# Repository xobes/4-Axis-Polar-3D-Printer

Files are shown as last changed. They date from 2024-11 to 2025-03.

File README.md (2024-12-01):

# 4 Axis Polar 3D Printer

This is my 4 axis, polar, "core-RΘ" 3D printer – an entirely new type of multi axis 3D printer designed from the ground up. 

Check out my [youtube video](https://www.youtube.com/watch?v=VEgwnhLHy3g) to see it in action!
Watch the video (https://www.youtube.com/watch?v=VEgwnhLHy3g)

### Slicer
A multi axis printer is pretty hopeless without a non-planar slicer, which is why I built this quick [radial slicer](https://github.com/jyjblrd/Radial_Non_Planar_Slicer) for the printer. This leverages the printer's rotating nozzle to print simple parts without supports, but there are some limitations to it which I cover in the YouTube video. I'm also working on an optimization based slicer which will be able to print any object without support so stay tuned for that!



### Assembly
You can view the [3d model online](https://a360.co/3VdXkRY) to see how to assemble the printer. Everything is 3D printable, however I got the extruder mount made out of metal by JLCPCB as there is quite a bit of torque on that part. I've also included the gerber files to make your own PCB buildplate, but a sheet of MDF wood would also work.

### BOM
Some links are included so you know what to get, but they are by no means the best source to get the parts.
| | Qty | | Note |
| --- | --- | --- | --- |
| Frame | | | |
| 2040 Extrusion 350mm | 1 | [Aliexpress](https://www.aliexpress.us/item/1005005037443914.html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) | |
| 2040 Extrusion 100mm | 1 | [Aliexpress](https://www.aliexpress.us/item/1005005037443914.html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) | |
| 2020 Extrusion 150mm | 1 | [Aliexpress](https://www.aliexpress.us/item/1005005037443914.html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) | |
| 2020 Extrusion 250mm | 1 | [Aliexpress](https://www.aliexpress.us/item/1005005037443914.html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) | |
| 2020 corner bracket | 10  | [Aliexpress](https://www.aliexpress.us/item/1005002883833150.html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) | |
| | | | |
| Hardware | | | |
| 2020 T Nuts | 50  | [Aliexpress](https://aliexpress.us/item/1005003023734101.html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) | |
| MGN9 250mm Rail | 1 | [Aliexpress](https://www.aliexpress.us/item/1005004908405311.html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) | |
| MGN12 250mm Rail | 2 | [Aliexpress](https://www.aliexpress.us/item/1005004908405311.html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) | |
| MGN9C Block | 2 | [Aliexpress](https://www.aliexpress.us/item/1005004908405311.html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) | |
| MGN12H Block | 2 | [Aliexpress](https://www.aliexpress.us/item/1005004908405311.html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) | |
| M4 Screw Set | | [Aliexpress](https://www.aliexpress.us/item/1005002109863123.html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) | |
| M3 Screw Set | | | Need 40mm screw |
| M3 Square Nut | 50  | [Aliexpress](https://www.aliexpress.us/item/1005001612157787.html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) | |
| MR85ZZ (5x8x2.5) | 4 | [Aliexpress](https://www.aliexpress.us/item/1005002702288640.html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) | B axis |
| 6810ZZ | 2 | [Aliexpress](https://www.aliexpress.us/item/32862403898.html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) | C axis |
| 5mm Rod 50mm length | | | B axis |
| 5mm Flange coupling | | | |
| 5x11x6 collet | 1 | [Aliexpress](https://www.aliexpress.com/item/1005005687346657.html?spm=a2g0o.order_list.order_list_main.270.6df81802pwJpHi) | B axis |
| | | | |
| Drive | | | |
| Nema 17 300mm Lead Screw | 1 | [Aliexpress](https://www.aliexpress.us/item/1005005575285492.html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) | |
| T8\*8 Lead Screw Nut | 1 | [Aliexpress](https://www.aliexpress.us/item/32957828816.html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) | |
| Nema 17 34mm | 3 | | |
| GT2 Belt Loop 410mm | 1 | | |
| GT2 Belt Loop 760mm | 1 | | |
| GT2 Pully 16T | 2 | [Aliexpress](https://www.aliexpress.us/item/1005004314084512.html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) | |
| GT2 Idler 16T w/o Teeth  | 4 | | |
| GT2 Pully 40T | 1 | | |
| GT2 Idler 16T w/ Teeth | 2 | [Aliexpress](https://www.aliexpress.us/item/32817328238.html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) | |
| | | | |
| Electronics | | | |
| Control Board | 1 | [Aliexpress](https://www.aliexpress.us/item/1005002372751834.html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) | |
| 24V 10A Power Brick | 1 | [Aliexpress](https://www.aliexpress.us/item/1005003088055215.html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) | |
| 5.5x2.5 plug | 1 | [Aliexpress](https://www.aliexpress.us/item/33034810979.html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) | |
| long nozzle | 1 | [Aliexpress](https://www.aliexpress.com/item/1005007437644929.html?spm=a2g0o.order_list.order_list_main.39.6df81802pwJpHi) | |
| aquarium pump | 1 | [Aliexpress](https://aliexpress.com/item/1005005987431203.html?spm=a2g0o.order_list.order_list_main.219.6df81802pwJpHi) | |
| BIQU H2 V2S extruder | 1 | [Aliexpress](https://www.aliexpress.com/item/1005002027842161.html?spm=a2g0o.order_list.order_list_main.274.6df81802pwJpHi) |

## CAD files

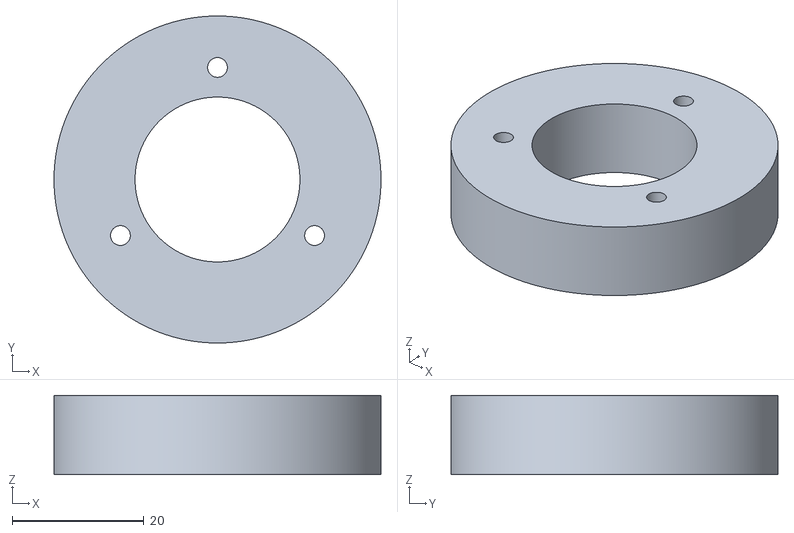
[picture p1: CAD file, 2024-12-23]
stl files/main body top.stl
49.6 x 49.6 x 12.0

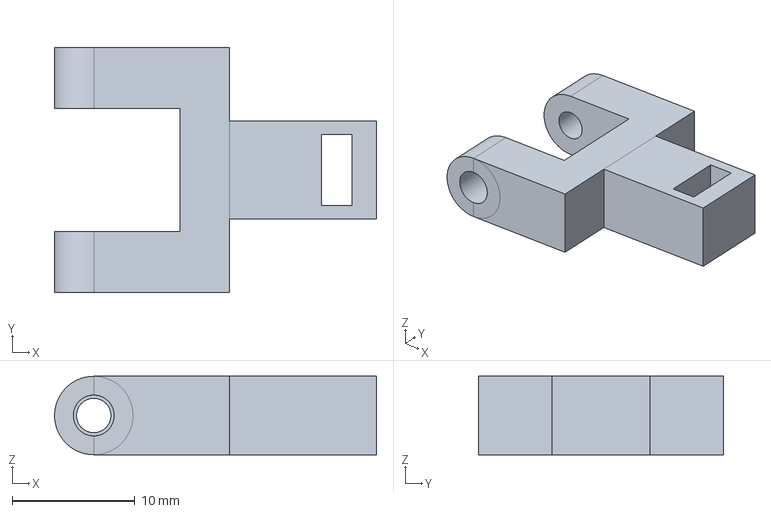
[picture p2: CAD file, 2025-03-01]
freecad_files/belt_loop_tensioner_slider.FCStd
26.2 x 20.0 x 6.40 mm

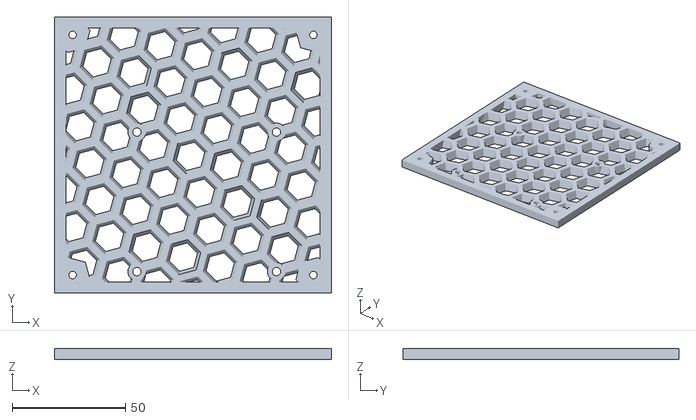
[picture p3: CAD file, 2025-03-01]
stl files/elec_box_top.stl
122.3 x 122.0 x 5.00

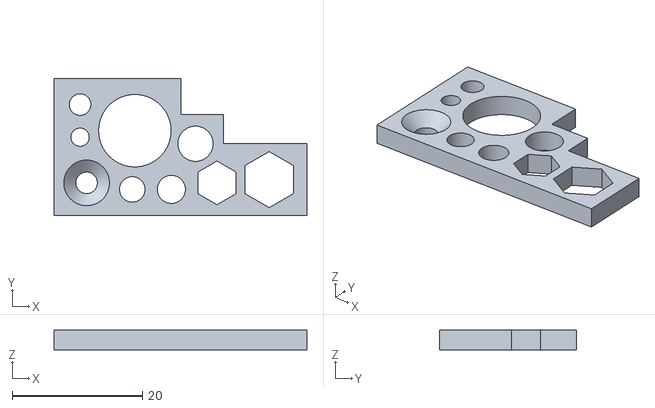
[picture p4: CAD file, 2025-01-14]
stl files/extra/hole_diameter_test_plate_2.stl
38.8 x 21.0 x 3.00

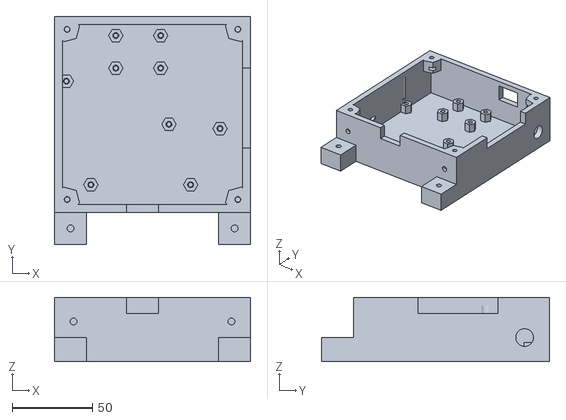
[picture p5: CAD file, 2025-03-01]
stl files/elec_box_bottom.stl
122.3 x 142.0 x 40.0

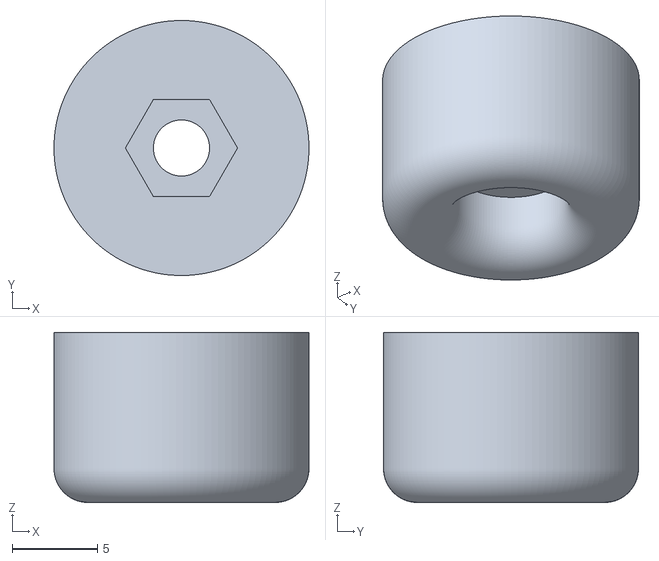
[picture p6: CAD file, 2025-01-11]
stl files/extra/m3_short_foot.stl
15.0 x 15.0 x 10.0

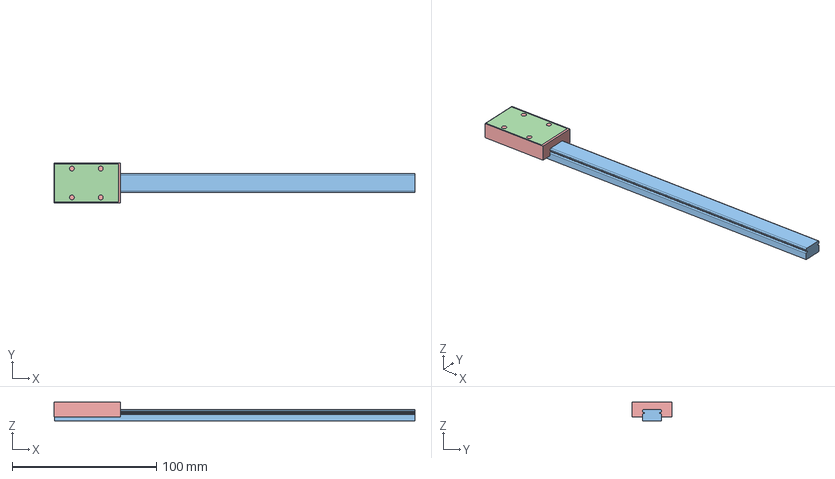
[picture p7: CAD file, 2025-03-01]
freecad_files/rails.FCStd
250.2 x 27.4 x 13.0 mm
slider_12_cutter_

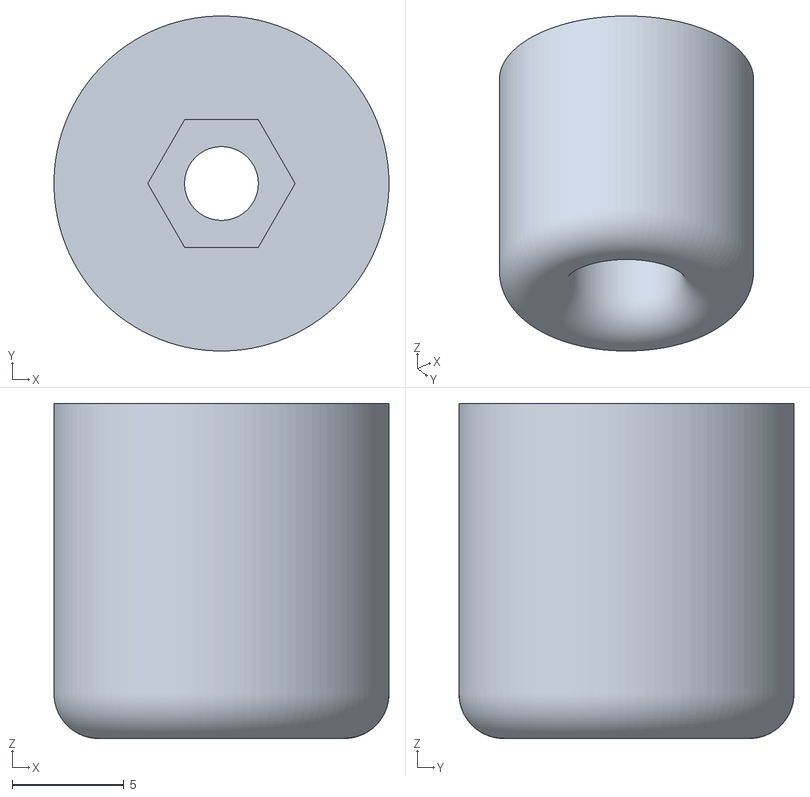
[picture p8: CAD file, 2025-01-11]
stl files/extra/m3_long_foot.stl
15.0 x 15.0 x 15.0

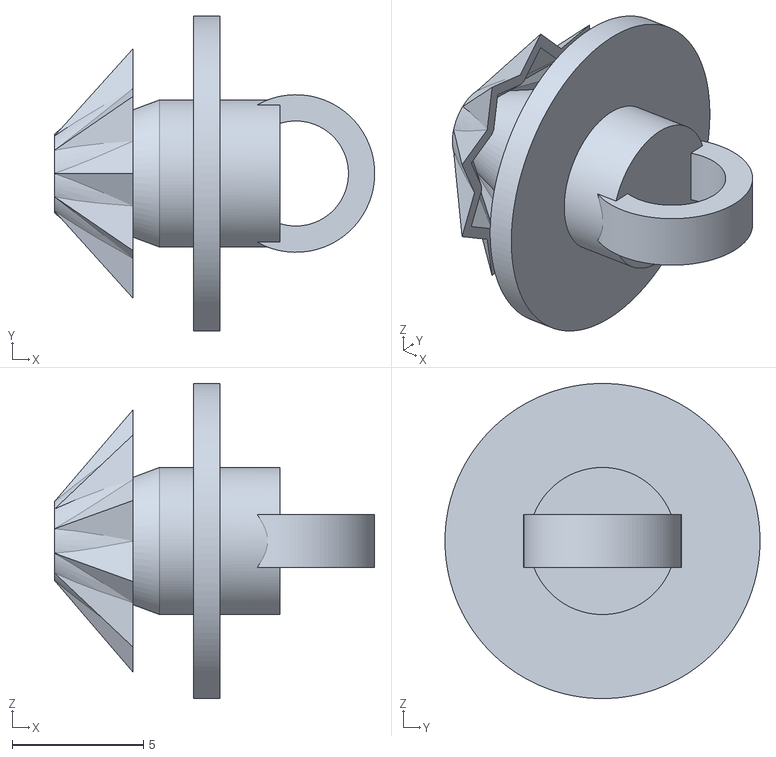
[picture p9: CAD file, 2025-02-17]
stl files/wire_clip_t2020_slider.stl
12.2 x 12.0 x 12.0

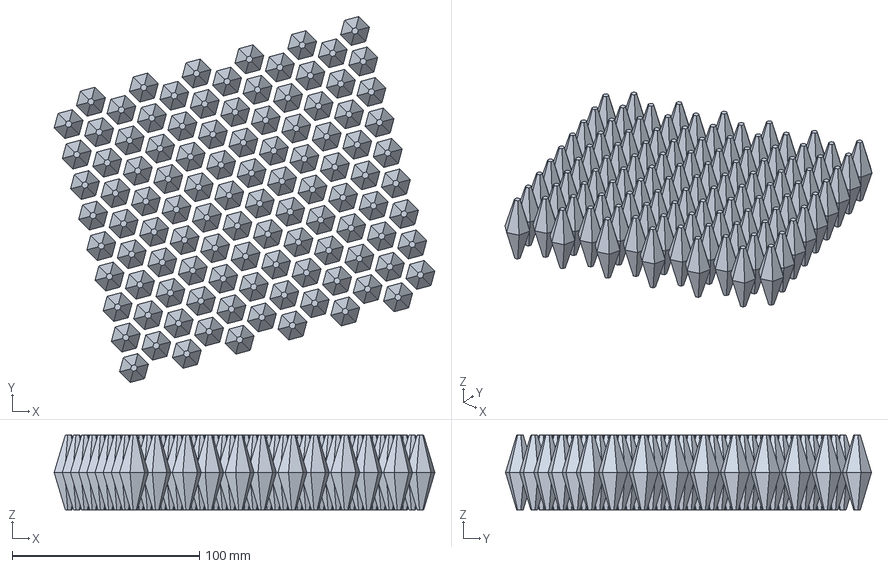
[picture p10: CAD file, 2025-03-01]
freecad_files/hex_mesh.FCStd
203.3 x 195.4 x 40.0 mm

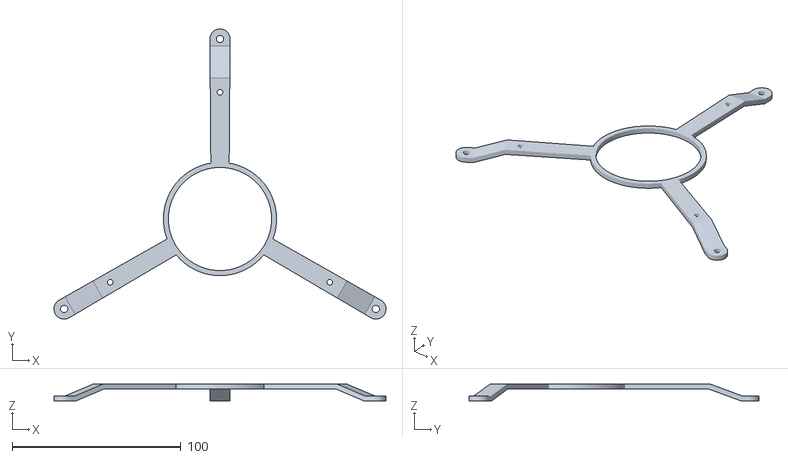
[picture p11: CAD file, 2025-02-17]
stl files/220mm_bed_expander.stl
196.5 x 171.8 x 10.0

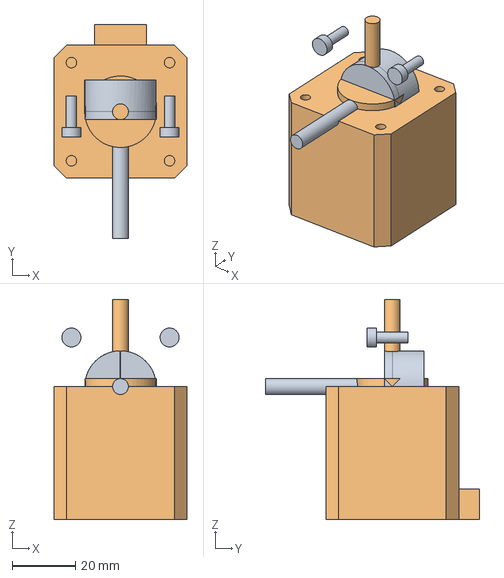
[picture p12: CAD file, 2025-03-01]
freecad_files/motors.FCStd
42.0 x 67.5 x 69.5 mm

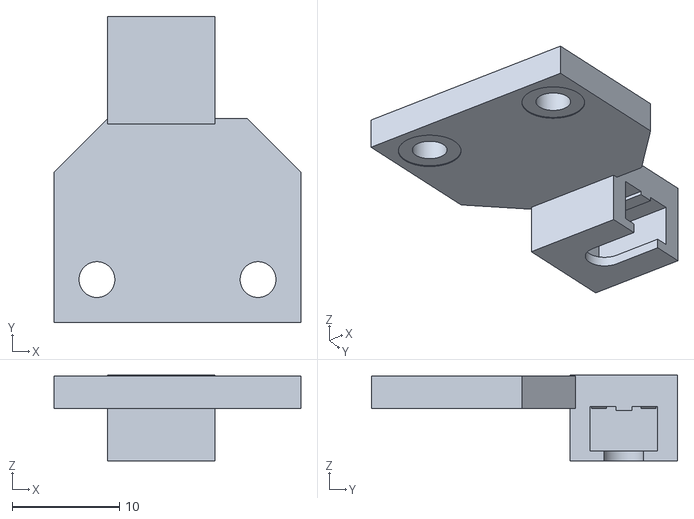
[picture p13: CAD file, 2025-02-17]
stl files/z_homing_switch_holder.stl
23.0 x 28.5 x 8.00

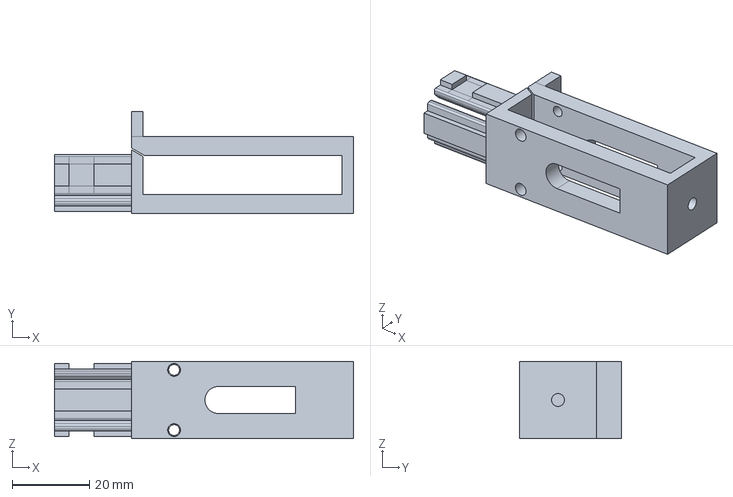
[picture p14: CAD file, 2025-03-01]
freecad_files/belt_loop_tensioner_body.FCStd
77.5 x 26.5 x 20.0 mm

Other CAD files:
stl files/extra/m4_long_foot.stl
stl files/220mm_bed_expander_third.stl
stl files/extra/hole_diameter_test_plate.stl
freecad_files/z_threaded_collet.FCStd
freecad_files/4_axis_polar_3d_printer.FCStd
freecad_files/b_axis_bracket.FCStd
freecad_files/bars.FCStd
freecad_files/build_plate.FCStd
freecad_files/c_axis_base.FCStd
freecad_files/c_axis_clamp.FCStd
freecad_files/cage.FCStd
freecad_files/electronics_box.FCStd
freecad_files/extruder.FCStd
freecad_files/extruder_mount.FCStd
freecad_files/global_parameters.FCStd
freecad_files/pulleys.FCStd
freecad_files/rods.FCStd
freecad_files/screws.FCStd
freecad_files/slip_ring.FCStd
freecad_files/switches.FCStd
freecad_files/test_parts.FCStd
freecad_files/x_limit_wire_rig.FCStd
freecad_files/z_axis_stopper.FCStd
freecad_files/z_cage_v1.FCStd
freecad_files/z_master_cage.FCStd
stl files/b axis bracket.stl
stl files/belt loop support 1.stl
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

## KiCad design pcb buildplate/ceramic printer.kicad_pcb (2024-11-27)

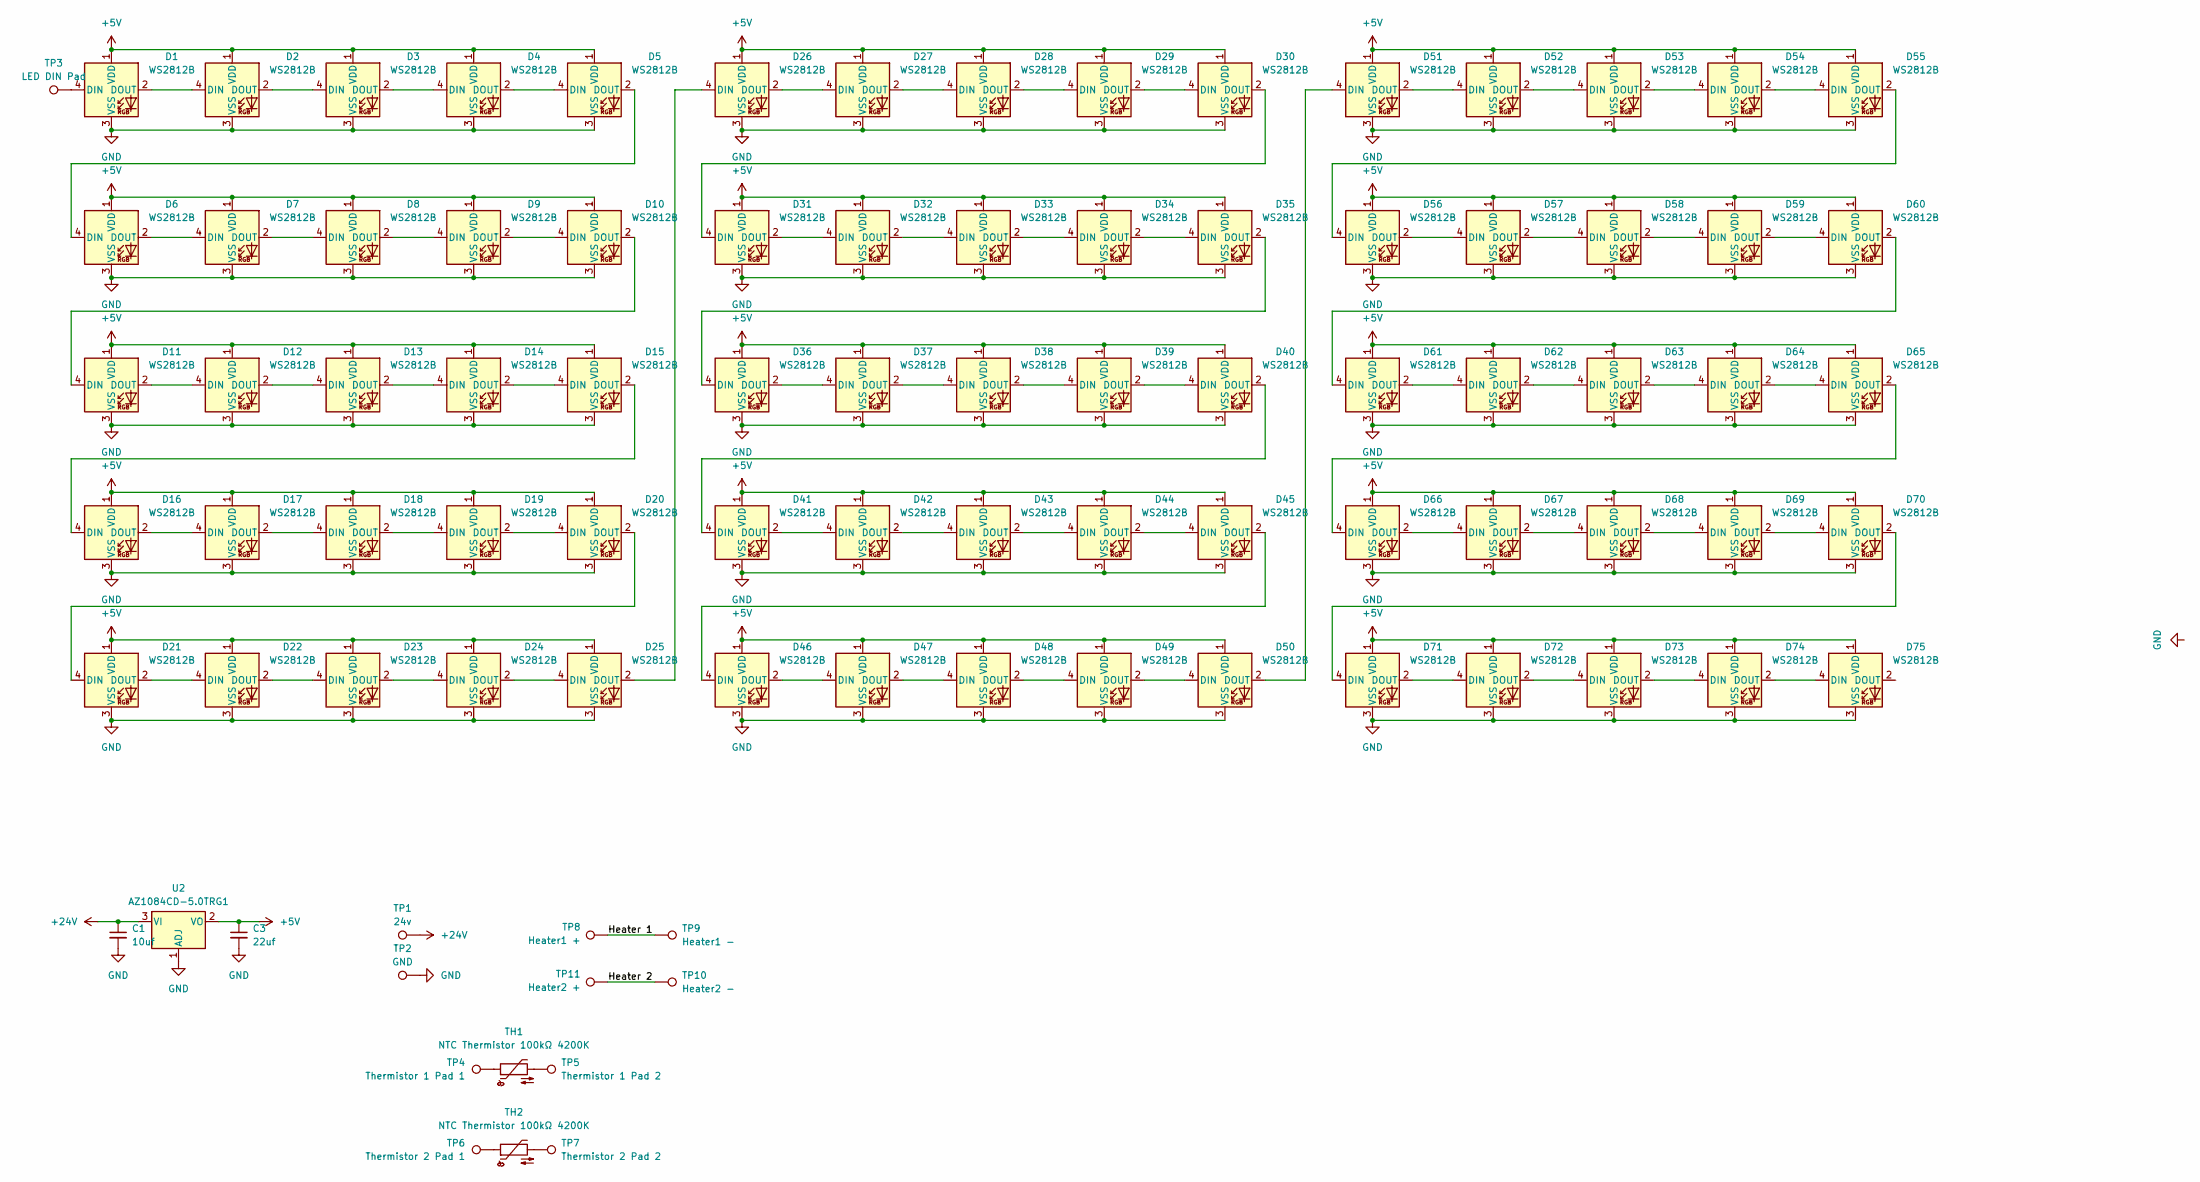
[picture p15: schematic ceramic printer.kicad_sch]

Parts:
C1: 10uf
C3: 22uf
D1, D2, D3, D4, D5, D6, D7, D8, D9, D10, D11, D12, D13, D14, D15, D16, D17, D18, D19, D20, D21, D22, D23, D24, D25, D26, D27, D28, D29, D30, D31, D32, D33, D34, D35, D36, D37, D38, D39, D40, D41, D42, D43, D44, D45, D46, D47, D48, D49, D50, D51, D52, D53, D54, D55, D56, D57, D58, D59, D60, D61, D62, D63, D64, D65, D66, D67, D68, D69, D70, D71, D72, D73, D74, D75: WS2812B; LED_WS2812B_PLCC4_5.0x5.0mm_P3.2mm
TH1, TH2: NTC Thermistor 100kΩ 4200K; R_0805_2012Metric_Pad1.20x1.40mm_HandSolder
TP1: 24v; TestPoint_Pad_4.0x4.0mm
TP2: GND; TestPoint_Pad_4.0x4.0mm
TP3: LED DIN Pad; TestPoint_Pad_2.5x2.5mm
TP4: Thermistor 1 Pad 1; TestPoint_Pad_2.0x2.0mm
TP5: Thermistor 1 Pad 2; TestPoint_Pad_2.0x2.0mm
TP6: Thermistor 2 Pad 1; TestPoint_Pad_2.0x2.0mm
TP7: Thermistor 2 Pad 2; TestPoint_Pad_2.0x2.0mm
TP8: Heater1 +; TestPoint_Pad_4.0x4.0mm
TP9: Heater1 -; TestPoint_Pad_4.0x4.0mm
TP10: Heater2 -; TestPoint_Pad_4.0x4.0mm
TP11: Heater2 +; TestPoint_Pad_4.0x4.0mm
U2: AZ1084CD-5.0TRG1; TO-252-2

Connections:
+5V: C3.1, D1.1 (VDD), D2.1 (VDD), D3.1 (VDD), D4.1 (VDD), D5.1 (VDD), D6.1 (VDD), D7.1 (VDD), D8.1 (VDD), D9.1 (VDD), D10.1 (VDD), D11.1 (VDD), D12.1 (VDD), D13.1 (VDD), D14.1 (VDD), D15.1 (VDD), D16.1 (VDD), D17.1 (VDD), D18.1 (VDD), D19.1 (VDD), D20.1 (VDD), D21.1 (VDD), D22.1 (VDD), D23.1 (VDD), D24.1 (VDD), D25.1 (VDD), D26.1 (VDD), D27.1 (VDD), D28.1 (VDD), D29.1 (VDD), D30.1 (VDD), D31.1 (VDD), D32.1 (VDD), D33.1 (VDD), D34.1 (VDD), D35.1 (VDD), D36.1 (VDD), D37.1 (VDD), D38.1 (VDD), D39.1 (VDD), D40.1 (VDD), D41.1 (VDD), D42.1 (VDD), D43.1 (VDD), D44.1 (VDD), D45.1 (VDD), D46.1 (VDD), D47.1 (VDD), D48.1 (VDD), D49.1 (VDD), D50.1 (VDD), D51.1 (VDD), D52.1 (VDD), D53.1 (VDD), D54.1 (VDD), D55.1 (VDD), D56.1 (VDD), D57.1 (VDD), D58.1 (VDD), D59.1 (VDD), D60.1 (VDD), D61.1 (VDD), D62.1 (VDD), D63.1 (VDD), D64.1 (VDD), D65.1 (VDD), D66.1 (VDD), D67.1 (VDD), D68.1 (VDD), D69.1 (VDD), D70.1 (VDD), D71.1 (VDD), D72.1 (VDD), D73.1 (VDD), D74.1 (VDD), D75.1 (VDD), U2.2 (VO)
+24V: C1.1, TP1.1, U2.3 (VI)
/Heater 1: TP8.1, TP9.1
/Heater 2: TP10.1, TP11.1
GND: C1.2, C3.2, D1.3 (VSS), D2.3 (VSS), D3.3 (VSS), D4.3 (VSS), D5.3 (VSS), D6.3 (VSS), D7.3 (VSS), D8.3 (VSS), D9.3 (VSS), D10.3 (VSS), D11.3 (VSS), D12.3 (VSS), D13.3 (VSS), D14.3 (VSS), D15.3 (VSS), D16.3 (VSS), D17.3 (VSS), D18.3 (VSS), D19.3 (VSS), D20.3 (VSS), D21.3 (VSS), D22.3 (VSS), D23.3 (VSS), D24.3 (VSS), D25.3 (VSS), D26.3 (VSS), D27.3 (VSS), D28.3 (VSS), D29.3 (VSS), D30.3 (VSS), D31.3 (VSS), D32.3 (VSS), D33.3 (VSS), D34.3 (VSS), D35.3 (VSS), D36.3 (VSS), D37.3 (VSS), D38.3 (VSS), D39.3 (VSS), D40.3 (VSS), D41.3 (VSS), D42.3 (VSS), D43.3 (VSS), D44.3 (VSS), D45.3 (VSS), D46.3 (VSS), D47.3 (VSS), D48.3 (VSS), D49.3 (VSS), D50.3 (VSS), D51.3 (VSS), D52.3 (VSS), D53.3 (VSS), D54.3 (VSS), D55.3 (VSS), D56.3 (VSS), D57.3 (VSS), D58.3 (VSS), D59.3 (VSS), D60.3 (VSS), D61.3 (VSS), D62.3 (VSS), D63.3 (VSS), D64.3 (VSS), D65.3 (VSS), D66.3 (VSS), D67.3 (VSS), D68.3 (VSS), D69.3 (VSS), D70.3 (VSS), D71.3 (VSS), D72.3 (VSS), D73.3 (VSS), D74.3 (VSS), D75.3 (VSS), TP2.1, U2.1 (ADJ)
unnamed: D1.4 (DIN), TP3.1
unnamed: D1.2 (DOUT), D2.4 (DIN)
unnamed: D2.2 (DOUT), D3.4 (DIN)
unnamed: D3.2 (DOUT), D4.4 (DIN)
unnamed: D4.2 (DOUT), D5.4 (DIN)
unnamed: D5.2 (DOUT), D6.4 (DIN)
unnamed: D6.2 (DOUT), D7.4 (DIN)
unnamed: D7.2 (DOUT), D8.4 (DIN)
unnamed: D8.2 (DOUT), D9.4 (DIN)
unnamed: D9.2 (DOUT), D10.4 (DIN)
unnamed: D10.2 (DOUT), D11.4 (DIN)
unnamed: D11.2 (DOUT), D12.4 (DIN)
unnamed: D12.2 (DOUT), D13.4 (DIN)
unnamed: D13.2 (DOUT), D14.4 (DIN)
unnamed: D14.2 (DOUT), D15.4 (DIN)
unnamed: D15.2 (DOUT), D16.4 (DIN)
unnamed: D16.2 (DOUT), D17.4 (DIN)
unnamed: D17.2 (DOUT), D18.4 (DIN)
unnamed: D18.2 (DOUT), D19.4 (DIN)
unnamed: D19.2 (DOUT), D20.4 (DIN)
unnamed: D20.2 (DOUT), D21.4 (DIN)
unnamed: D21.2 (DOUT), D22.4 (DIN)
unnamed: D22.2 (DOUT), D23.4 (DIN)
unnamed: D23.2 (DOUT), D24.4 (DIN)
unnamed: D24.2 (DOUT), D25.4 (DIN)
unnamed: D25.2 (DOUT), D26.4 (DIN)
unnamed: D26.2 (DOUT), D27.4 (DIN)
unnamed: D27.2 (DOUT), D28.4 (DIN)
unnamed: D28.2 (DOUT), D29.4 (DIN)
unnamed: D29.2 (DOUT), D30.4 (DIN)
unnamed: D30.2 (DOUT), D31.4 (DIN)
unnamed: D31.2 (DOUT), D32.4 (DIN)
unnamed: D32.2 (DOUT), D33.4 (DIN)
unnamed: D33.2 (DOUT), D34.4 (DIN)
unnamed: D34.2 (DOUT), D35.4 (DIN)
unnamed: D35.2 (DOUT), D36.4 (DIN)
unnamed: D36.2 (DOUT), D37.4 (DIN)
unnamed: D37.2 (DOUT), D38.4 (DIN)
unnamed: D38.2 (DOUT), D39.4 (DIN)
unnamed: D39.2 (DOUT), D40.4 (DIN)
unnamed: D40.2 (DOUT), D41.4 (DIN)
unnamed: D41.2 (DOUT), D42.4 (DIN)
unnamed: D42.2 (DOUT), D43.4 (DIN)
unnamed: D43.2 (DOUT), D44.4 (DIN)
unnamed: D44.2 (DOUT), D45.4 (DIN)
unnamed: D45.2 (DOUT), D46.4 (DIN)
unnamed: D46.2 (DOUT), D47.4 (DIN)
unnamed: D47.2 (DOUT), D48.4 (DIN)
unnamed: D48.2 (DOUT), D49.4 (DIN)
unnamed: D49.2 (DOUT), D50.4 (DIN)
unnamed: D50.2 (DOUT), D51.4 (DIN)
unnamed: D51.2 (DOUT), D52.4 (DIN)
unnamed: D52.2 (DOUT), D53.4 (DIN)
unnamed: D53.2 (DOUT), D54.4 (DIN)
unnamed: D54.2 (DOUT), D55.4 (DIN)
unnamed: D55.2 (DOUT), D56.4 (DIN)
unnamed: D56.2 (DOUT), D57.4 (DIN)
unnamed: D57.2 (DOUT), D58.4 (DIN)
unnamed: D58.2 (DOUT), D59.4 (DIN)
unnamed: D59.2 (DOUT), D60.4 (DIN)
unnamed: D60.2 (DOUT), D61.4 (DIN)
unnamed: D61.2 (DOUT), D62.4 (DIN)
unnamed: D62.2 (DOUT), D63.4 (DIN)
unnamed: D63.2 (DOUT), D64.4 (DIN)
unnamed: D64.2 (DOUT), D65.4 (DIN)
unnamed: D65.2 (DOUT), D66.4 (DIN)
unnamed: D66.2 (DOUT), D67.4 (DIN)
unnamed: D67.2 (DOUT), D68.4 (DIN)
unnamed: D68.2 (DOUT), D69.4 (DIN)
unnamed: D69.2 (DOUT), D70.4 (DIN)
unnamed: D70.2 (DOUT), D71.4 (DIN)
unnamed: D71.2 (DOUT), D72.4 (DIN)
unnamed: D72.2 (DOUT), D73.4 (DIN)
unnamed: D73.2 (DOUT), D74.4 (DIN)
unnamed: D74.2 (DOUT), D75.4 (DIN)
unnamed: TH1.1, TP4.1
unnamed: TH1.2, TP5.1
unnamed: TH2.1, TP6.1
unnamed: TH2.2, TP7.1

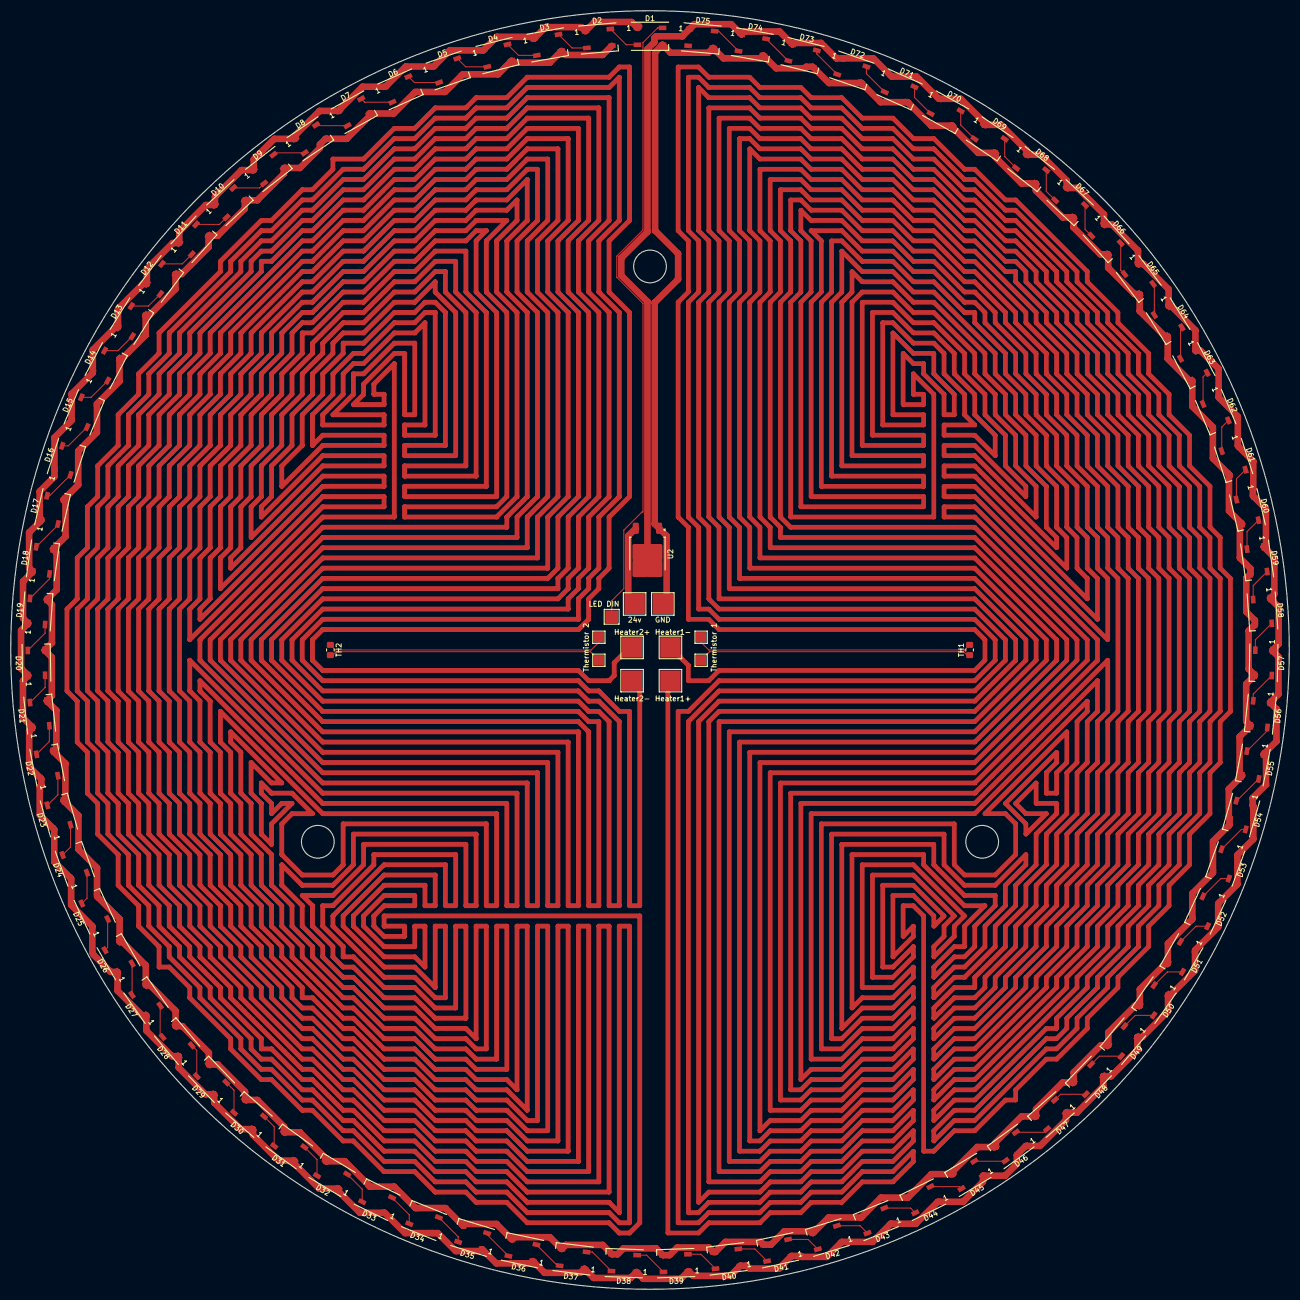
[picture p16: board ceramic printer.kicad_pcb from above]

Board: 2 copper layers, 250.0 x 250.0 mm, 89 parts (0 on the bottom side), 84 nets.

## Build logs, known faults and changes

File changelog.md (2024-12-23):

2024-12-04
Re-exported all files with higher poly count
Rotate models in f360 before export to default slicer orientation

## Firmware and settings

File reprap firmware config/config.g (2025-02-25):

; Configuration file for Fly-E3-Pro-v3 (firmware version 3.5)
; executed by the firmware on start-up
;
; generated by RepRapFirmware Configuration Tool v3.5.0-STM32+1 on Sun Feb 02 2025 20:10:53 GMT-0600 (Central Standard Time)

; General preferences
G90                                                  ; send absolute coordinates...
M83                                                  ; ...but relative extruder moves
M550 P"Stinger"                                      ; set printer name

; Network
M552 S1                                              ; enable network
M586 P0 S1                                           ; enable HTTP
M586 P1 S0                                           ; disable FTP
M586 P2 S0                                           ; disable Telnet

; define the relay pin and turn it on deliberately, later M81/M80 will work to power cycle drivers
M80 C"PSON"

; Drives
M84 S30                                              ; Set idle timeout

; Configure printer as 4-axis variant:
; M98 P"to4axis.g" ; the gcode examples require polar...
M98 P"topolar.g" 

; Accelerometer -- OPTIONAL
; M955 P0 C"PB_2+PA_10" I46

; Input shaping
; M593 P"zvddd" F38

; Temperature sensors:
M308 S2 P"boardtemp" Y"thermistor" A"Fly Board Temp" T100000 B4092 
M308 S0 P"e0temp" Y"thermistor" A"Extruder" T100000 B4956 C1.587780e-7 ; configure sensor 0 as thermistor on pin e0temp
M308 S1 P"bedtemp" Y"thermistor" T100000 A"Bed"

; Heaters
M950 H0 C"e0heat" T0                                       ; create nozzle heater output on e0heat and map it to sensor 0
M307 H0 R2.703 K0.364:0.000 D11.05 E1.35 S1.00 B0 V23.7    ; pwm config from autotune
M143 H0 S270                                               ; set temperature limit for heater 0
M302 P0                                                    ; disallow cold extrudes

; Bed
M950 H1 C"bed" T1                                          ; create nozzle heater output on e0heat and map it to sensor 0
; M307 H1 R2.703 K0.364:0.000 D11.05 E1.35 S1.00 B0 V23.7    ; pwm config from autotune
M143 H1 S90                                                ; set temperature limit for bed

; Fans
M950 F0 C"fan1"                                            ; create fan 0 on pin fan0 and set its frequency
M106 P0 S0 H0 T50                                          ; set fan 0 value. Thermostatic control is turned on

M950 F1 C"!PA_7" Q50                                       ; create fan 1 on pin PA_0

; Tools
M563 P0 D0 F0 H0                                           ; define tool 0
G10 P0 X0 Y0 Z0                                            ; set tool 0 axis offsets
G10 P0 R0 S0                                               ; set initial tool 0 active and standby temperatures to 0C
T0                                                         ; select tool

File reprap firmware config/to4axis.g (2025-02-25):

; Notes on physical configuration:
; C (Driver 0) is the bed, Positive is ????  CW/CCW?
; X (Driver 1) is BOTTOM \_ The combination of Driver 1 and 2 drives "B" (extruder angle) and "X" in and out radially
; B (Driver 2) is TOP    /  ...B is Positive DOWN from homing position, X is Positive AWAY from bed Center.
; Z (Driver 4) is obvious..., Positive is UP
; Extruder (Driver 3) is obvious as well.

; Drives
M584 C0 Z4 X1 B2 E3 S0         ; set drive mapping 4 axis. treat all as linear axes in feedrate calculations (have to use inverse time feed rate in gcode)
M569 P0 S1                     ; physical drive 0 (C) goes forwards using TMC2209 driver timings
M569 P1 S0  D3 V40             ; physical drive 1 (Bottom) goes reverse using TMC2209 driver timings
M569 P2 S0  D3 V40             ; physical drive 2 (Top) goes reverse using TMC2209 driver timings
M569 P3 S0                     ; physical drive 3 (E) goes reverse using TMC2209 driver timings
M569 P4 S1                     ; physical drive 4 (Z) goes forwards using TMC2209 driver timings

M350 C16       X16       Z16      B16       E16      I1  ; configure microstepping with interpolation
M92  C88.8888  X100.00   Z400.00  B100.00   E932.00      ; set steps per mm
M566 C600.00   X600.00   Z600.00  B600.00   E300.00      ; set maximum instantaneous speed changes (mm/min)
M203 C21600.00 X20000.00 Z8000.00 B21600.00 E3600.00     ; set maximum speeds (mm/min)
M201 C2000.00  X2000.00  Z1500.00 B2000.00  E2000.00     ; set accelerations (mm/s^2)
M906 C1500     X1500     Z1000    B1500     E800     I30 ; set motor currents (mA) and motor idle factor (in percent)

; Axis Limits
; Note: The values specified set the software limits for axis travel in the specified direction. 
; Note: The axis limits you set are also the positions assumed when an endstop is triggered.
; ... Therefore:
;     - Endstop for X MAXima is the value set while homing. i.e. Positive is from center of Bed toward Z axis tower
;     - Endstop for B MINima is the value set while homing. i.e. Positive from home is down toward Bed.
;     - Endstop for Z MINima is the bed surface itself (by definition zero)
;     - C has no endstops or minima/maxima, hence the really large values
M208 C-20000000  X-37.5 Z0    B-90.9  S1          ; set axis minima
M208 C20000000   X98.5  Z200  B90     S0          ; set axis maxima

; Configure endstops and Z-Probe settings
; Z -------------------------------------
M558 P5 C"!e1stop" H5 F500   ; set Z probe type to "switch" and the dive height + speeds
G31 P500 X0 Y0 Z-22.25       ; set Z probe trigger value, offset and trigger height
M574 Z1 S2                   ; use z-probe for limit sensing on lower z-limit while homing
; X -------------------------------------
M574 X2 S1 P"!xstop"         ; configure limit switch endstop for high end on X
; B -------------------------------------
M574 B1 S3           	     ; configure sensorless endstop for low end on B
M915 B R0 F0 S60             ; Configure motor stall detection for the B-axis, R0=no action, F0=unfiltered, S=threshhold

; Define Kinematics
; Driver:1:-:4:2:0  1:-:4:2 :0  1:-:4:2:0           1:-:4:2          :0
;   Axis:X:Y:Z:B:C  X:Y:Z:B :C  X:Y:Z:B:C           X:Y:Z:B          :C
M669 K0 C0:0:0:0:1 X1:0:0:-1:0 Z0:0:1:0:0 B0.22222222:0:0:0.222222222:0 ; 4 axis control
; X and Z coordinates are in millimeters
; B coordinates are in degrees
; C coordinates are ... ??? TBD

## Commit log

2024-12-05 Fixed orientation of STLs to be explicit about print orientation. exported with higher poly count
    [belt loop support 1.stl, belt loop support 2.stl, belt loop support plate.stl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]
2025-01-03 add rrf config
    [config.g, homeall.g, to4axis.g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]
2025-01-03 add cooling duct stls
    [extruder cooling duct tube adapter.stl, extruder cooling duct.stl]
2025-01-03 more config files
    [config.g, homeb.g, homec.g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]
2025-01-09 untested and unfinished, just to share progress
    [4-axis_polar_3d_printer.FCStd, hole_diameter_test_plate.stl, hole_diameter_test_plate_2.stl]
2025-01-10 tweaks based on feedback and proper modelling of extruder and set screws
    [M3 T nut.stl]
2025-01-10 tweaked dimensions on slot and slider (plate) for tensioner to allow for idler pulley flanges
    [4-axis_polar_3d_printer.FCStd, b axis bracket.stl, belt loop tensioner 1.stl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]
2025-01-11 added feet
    [m3_long_foot.stl, m3_short_foot.stl, m3_t_nut.stl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]
2025-01-14 lots of freecad updates, z-axis modelled, working on more changes
    [M3 T nut.stl, belt loop tensioner 1.stl, hole_diameter_test_plate_2.stl]
2025-01-21 Cage parted out into front, back, sides, etc. and file broken out into parts for sake of memory management.
    [4-axis_polar_3d_printer.FCStd, 4_axis_polar_3d_printer.FCStd]
2025-01-21 ready to move set screws...
    [4_axis_polar_3d_printer.FCStd, bars.FCStd, extruder.FCStd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]
2025-01-21 updated all copies into links for these files
    [b_axis_bracket.FCStd, bars.FCStd, belt_loop_tensioner_body.FCStd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]
2025-01-25 more work on getting things into individual files
    [4_axis_polar_3d_printer.FCStd, b_axis_bracket.FCStd, belt_loop_tensioner_body.FCStd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]
2025-01-29 i think i got it all moved around and the cage v1 with hex pattern sorted out!
    [4_axis_polar_3d_printer.FCStd, b_axis_bracket.FCStd, bars.FCStd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]
2025-02-01 added c-axis tensioner and beefier z-stop (need 2)
    [4_axis_polar_3d_printer.FCStd, bars.FCStd, belt loop tensioner 1.stl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]
2025-02-06 Added electronics box (needs tweaking), and a bridge from the X/B pulleys similar to the original design
    [4_axis_polar_3d_printer.FCStd, b_axis_bracket.FCStd, bars.FCStd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]
2025-02-06 adjust dimensions of the stud spacer to wrap around the bar
    [pulley_stud_spacer_a.stl, screws.FCStd, z_master_cage.FCStd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]
2025-02-17 added switch holders for limit switches, updates to 2020 bar profile, added wire slider things -- need to fix overlapp stl problem.
    [220mm_bed_expander.stl, 220mm_bed_expander_third.stl, 4_axis_polar_3d_printer.FCStd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]
2025-02-17 replaced cylider with ring for goood stl
    [wire_clip_t2020_slider.stl, x_limit_wire_rig.FCStd]
2025-02-22 freecad and stl updates, added slipring and played with some x-axis-wire-rigging, didn't work though.
    [c axis clamp.stl, c_axis_clamp.FCStd, screws.FCStd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]
2025-02-22 got homing working for my wiring/physical setup
    [bed.g, config.g, homeall.g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]
2025-02-25 got polar version working
    [config.g, homeall.g, homeb.g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]
2025-03-01 updated electrical box to support fan, switch and have feet to connect to metal differently
    [4_axis_polar_3d_printer.FCStd, b_axis_bracket.FCStd, belt_loop_tensioner_body.FCStd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]
